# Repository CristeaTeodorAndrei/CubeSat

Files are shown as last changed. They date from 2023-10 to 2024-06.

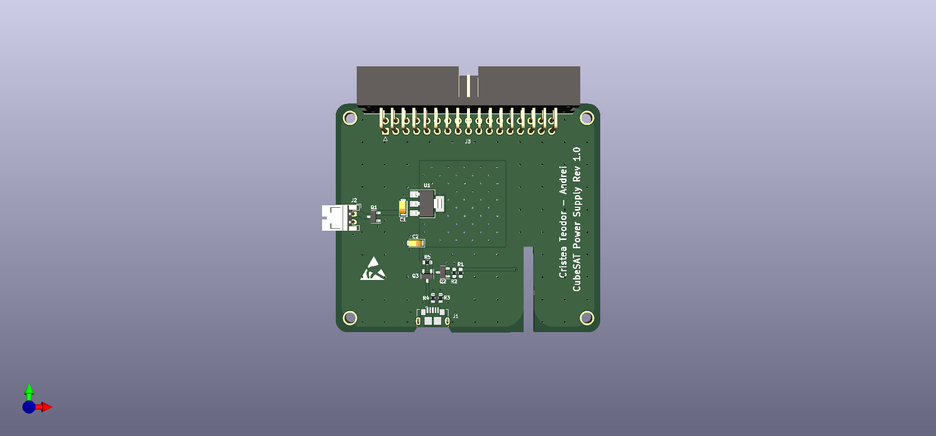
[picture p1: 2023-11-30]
Photos/PSB.png

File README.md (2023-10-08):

# CubeSat

## Introduction

### About CubeSat

A CubeSat is a compact but sophisticated space platform, meticulously engineered to achieve its scientific goals. These miniaturised satellites are created with precision and purpose, representing a cost-effective and efficient approach to space exploration. Their primary role involves specific scientific, technological or educational missions. <br>
Equipped with payloads, sensors and specialised instruments, CubeSats are deployed to collect critical data, monitor phenomena or conduct experiments in space. Their modular nature allows for versatility, enabling CubeSats to address a wide range of research objectives, from observing Earth to studying cosmic phenomena. <br>
They contribute to advancing our understanding of the cosmos, demonstrating that innovation can thrive even within the confines of a compact form factor.

### About the project

The project was developed with the objective of understanding the complexity of space systems, approaching the different problems that arise in this field and solving them in the most energy and cost efficient way. <br>
The future of this project consists in creating a stable platform that allows future improvements so that young students in this domain can develop.

## CubeSat specifications

### Hardware specs

    1. Raspberry PI 4 Model B
    2. MPU6050 Accelerometer and Gyroscope Sensor
    3. BMP280 Pressure Sensor
    4. Raspberry Pi Camera Module 2
    5. NRF20L01 Wireless Module
    6. Battery System UPS 

### Software specs

OBSW was developed in Python, and the operating system on which the software runs is Raspberian on which some software optimizations have been applied.  <br>
The project is structured in 4 phases:

- Activating Remote Control Phase
- Optimization phase
- Testing phase
- OBSW phase

<br>
Each of these phases has a well-defined objective and must be fulfilled before the final code runs.

## Guideline

### Activating Remote Control Phase

Keep in mind that each script that will run will be sent as a command through the GCM. <br>

Power on the GCM, run the script and open the receiver Interface.

- The Interface should prompt a successful connection message.
- A warning message should appear to notify the failure to connect with the OBC. <br>

Power on the OBC.

- Both GREEN and RED LEDs should be ON indicating that OBC is active and ready for requests.
- A succesful connection message should appear on GCM's Interface to ensure that communcations with the OBC is active and can proceed to the optimization phase.

<br>
GCM will try to connect with the OBC every 5 seconds.

### Optimization Phase

In order to reduce energy usage and ensure efficient performance of the whole system, a number of optimizations have been implemented:

- Deactivating Wi-Fi Module
- Deactivating Bluetooth Module
- Deactivating Update Module
- Deactivating UI

By requesting the OBC to run the script <b> Optimization.py</b> via GCM all of those optimizations will be applied and after that the OBC will reboot. <br>
After restarting the system, the GREEN LED will turn ON and RED LED OFF to indicate successful optimization and a confirmation message should appear in GCM's Interface. <br>
<br>
OBC can proceed to the testing phase.

### Testing Phase

By requesting the OBC to run the script <b>Test.py</b>, the OBC begins testing sequence and a custom TM is sent back to the GCM that indicates the sensors has been detected. <br>
If the RFM is not working or is not responding the RED LED will blink continuously.<br>
If the RFM is working the GREEN LED will blink continuously and a TM will be send to the GCM with the following format:

- [0x00, 0x00, 0x00, 0x00]

TM's params should have the following values:

1. (First) 0x00 - MPU6050 has been detected.

- 0x01 - MPU6050 has not been detected.

2. (Second) 0x00 - BMP280 has been detected.

- 0x01 - BMP280 has not been detected.

3. (Third) 0x00 - Camera Module has been detected.

- 0x01 - Camera Module has not been detected.

4. (Fourth) 0x00 - Power supply voltage is nominal.

- 0x05 - The OBC is undervoltage and the power supply should be verified.

<br>
If the TM's values are not nominal OBSW will repeat the test every 5 seconds. <br>
OBC can proceed to the running phase or main code.

### Running phase

In the phase of running the main code all CubeSat components should work according to the parameters.
<br><br>
By requesting the OBC to run the main code <b>OBSW.py</b> nominal TMs should appear in GCM's Interface. <br>
As discussed in the SDCard chapter before the CubeSat leaves the range of the GCM the OBSW will send a warning message that it will soon disconnect and the data will be written locally. 
<br><br>
That's the final state for the CubeSat before the flight. 

### TMTC Format

A nominal TM should have the following format:

- [TimeStamp, Voltage, Temperature, Load, AccX, AccY, AccZ, GyroX, GyroY, GyroZ, Altitude, Pressure]

TM's params should have the following values:

1. <b>TimeStamp</b> [seconds] float (Eg. 1.00) and represent the relative time.
2. <b>Voltage</b> float (Eg. 1.2) and represent the core voltage.
3. <b>Temperature</b>[degrees] float (Eg. 57.01) and represent the OBC's temperature.
4. <b>Load</b> [%] integer (Eg. 5%) and represent the OBC's load.
5. <b>Acceleration{X,Y,Z}</b>[m/s^2] float (Eg. 10.32) and represent the acceleration on each axis.
6. <b>Gyro{X,Y,Z}</b>[deg/s] float (Eg. 11.01) and represent the rotation on each axis.
7. <b>Altitude</b>[meters] integer (Eg. 1100) and represent the altitude of the CubeSat.
8. <b>Pressure</b>[hPa] float (Eg. 1013.89) and represent the pressure applied to the CubeSat. <br>

<br>
One TM is sent every 5 seconds. <br>
Keep in mind that TMTC will only be available for a period of time until the CubeSat moves out of range of the GCM.

### SDCard

Cubesat will have a Raspberry Pi Camera Module 2 connected and the record will be stored on the SD Card. <br>
Because the RFM allows communication over a relatively short distance with the GCM the flight parameters will be stored on the OBC's internal SD Card. <br>
The OBSW will notify the approaching maximum range and detect the loss of GCM connection, and the data will be passed in .txt format. <br>

## Acronyms

- OBSW - OnBoard Software
- UI - User Interface
- OBC - OnBoard Computer
- TMTC - Telemetry/Telecommand
- GCM - Ground Communication Module
- RFM - Radio Frequency Module

## About me

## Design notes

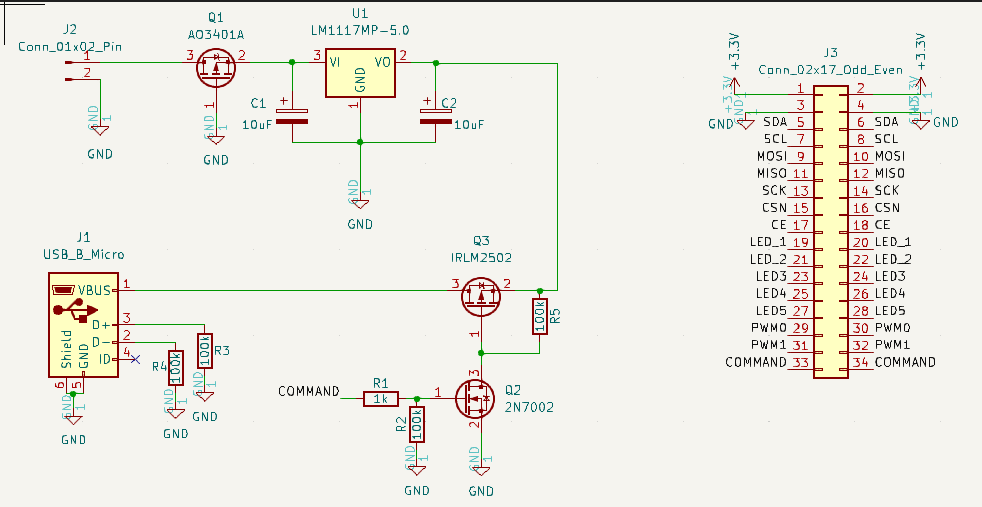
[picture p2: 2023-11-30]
Photos/Schematic_PSB.png

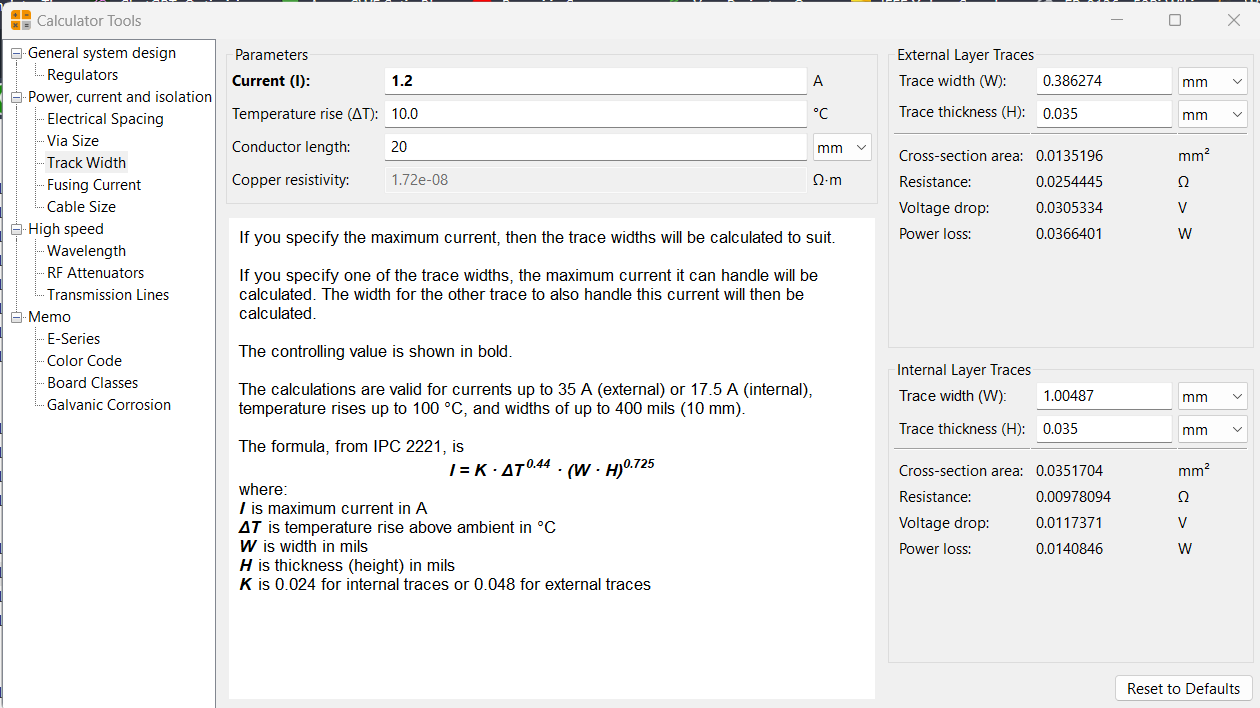
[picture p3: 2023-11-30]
Photos/Power_PSB.png

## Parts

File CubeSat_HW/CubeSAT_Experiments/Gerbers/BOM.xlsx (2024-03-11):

Comment | Designator | Footprint | JLCPCB Part #（optional）
D1 | D1 | LED_0603_1608Metric | C2286
D2 | D2 | LED_0603_1608Metric | C434449
220R | R1 | R_0603_1608Metric | C22962
180R | R2 | R_0603_1608Metric | C22828

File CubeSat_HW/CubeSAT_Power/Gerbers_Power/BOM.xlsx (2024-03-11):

Comment | Designator | Footprint | JLCPCB Part #（optional）
AO3401A | Q1 | SOT-23 | C15127
100k | R4, R3, R2, R5 | R_0603_1608Metric | C25803
LM1117MP-5.0 | U1 | SOT-223-3_TabPin2 | C41202
1k | R1 | R_0603_1608Metric | C21190
10uF | C1, C2 | CP_EIA-3216-18_Kemet-A | C7171
IRLM6402 | Q3 | SOT-23 | C347504
2N7002 | Q2 | SOT-23 | C8545
Micro USB | J1 | Micro USB | C381144

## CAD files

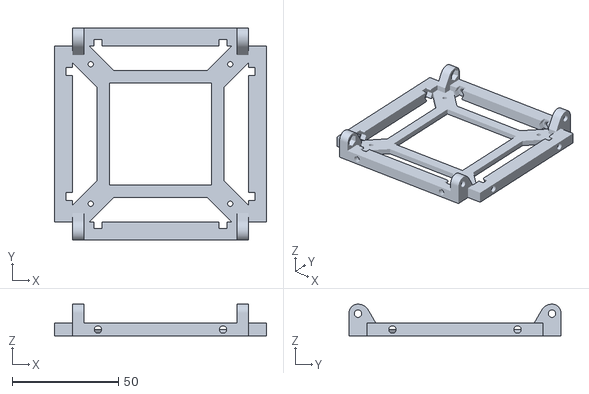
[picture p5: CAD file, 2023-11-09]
CubeSat_3D/Cubesat_Bottom_Frame.stl
100.0 x 100.0 x 15.0

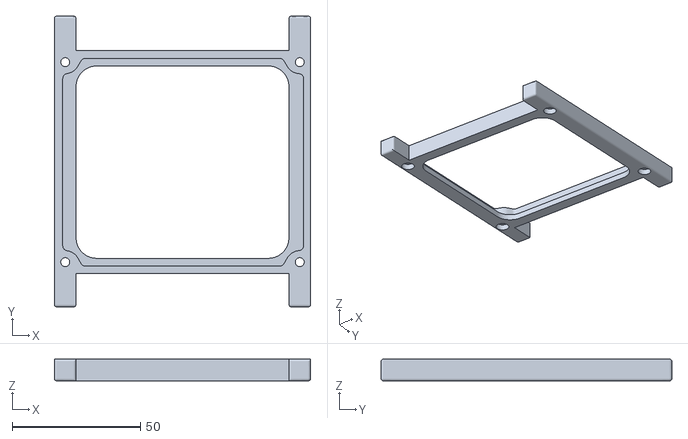
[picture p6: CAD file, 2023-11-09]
CubeSat_3D/Cubesat_Side_Frame_Plain.stl
100.0 x 113.5 x 8.50

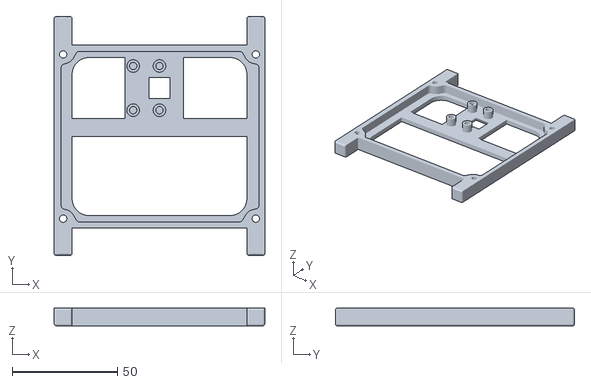
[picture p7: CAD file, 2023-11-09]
CubeSat_3D/Cubesat_RaspbiCam_Frame.stl
100.0 x 113.5 x 8.50

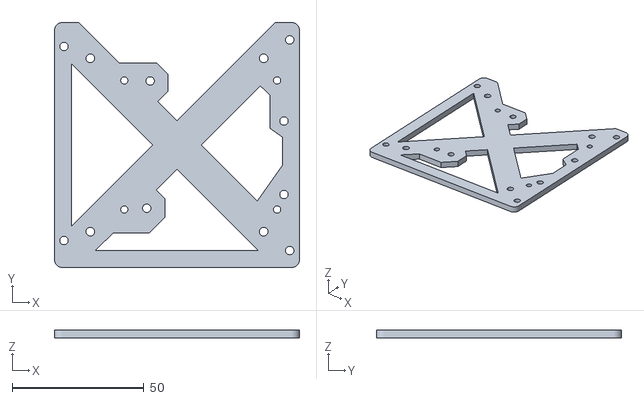
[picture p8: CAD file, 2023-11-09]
CubeSat_3D/Cubesat_Adaptor_Mount.stl
93.0 x 93.0 x 3.00

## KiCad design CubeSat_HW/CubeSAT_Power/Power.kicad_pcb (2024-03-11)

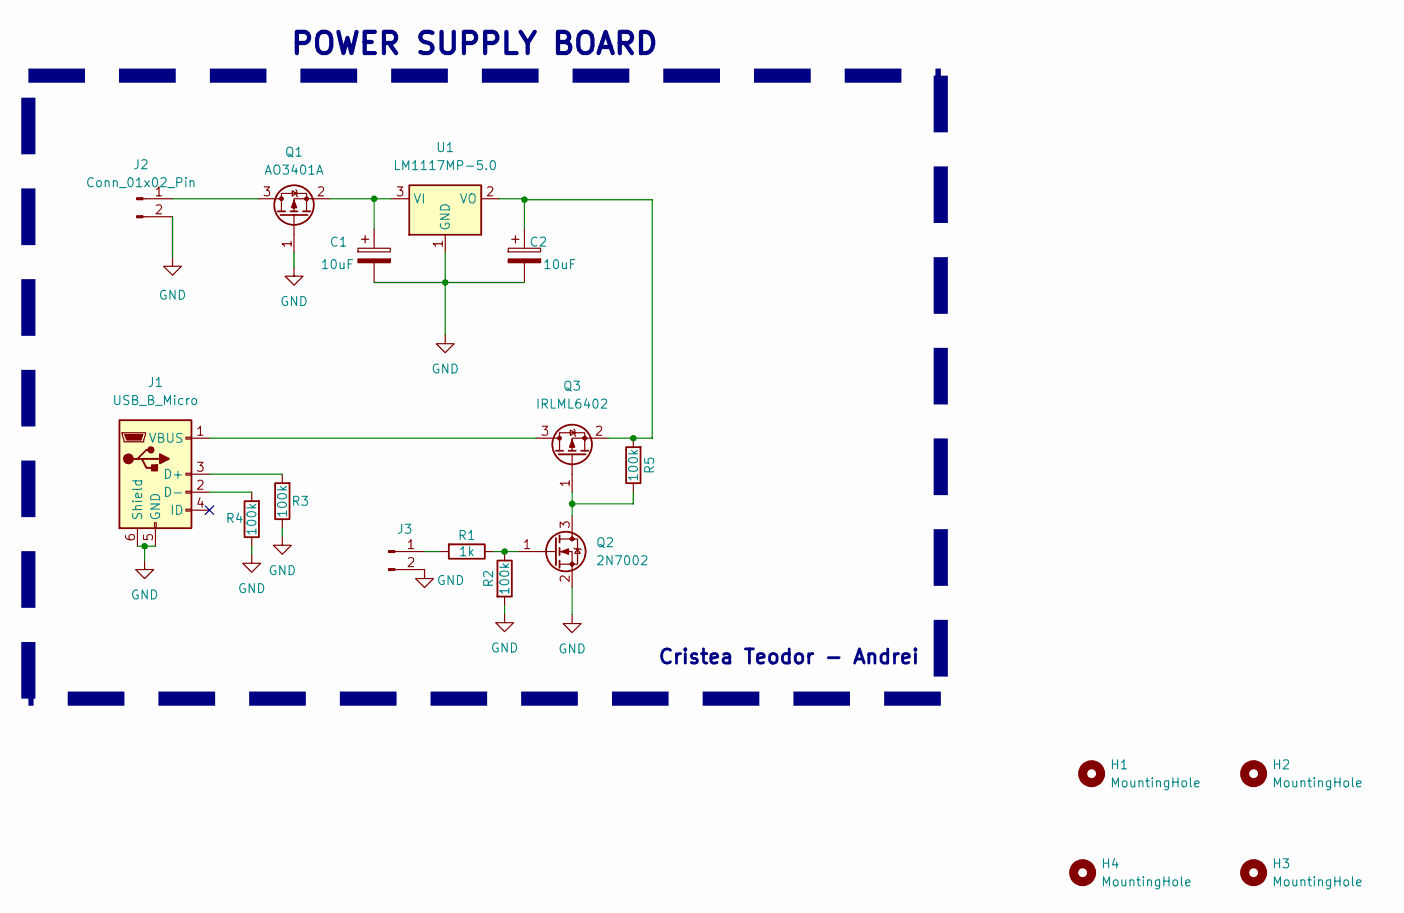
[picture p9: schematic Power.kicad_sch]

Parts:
C1, C2: 10uF; CP_EIA-3216-18_Kemet-A
H1, H2, H3, H4: MountingHole; MountingHole_2.7mm
J1: USB_B_Micro; USB_Micro-B_GCT_USB3076-30-A
J2, J3: Conn_01x02_Pin; PinHeader_1x02_P2.54mm_Vertical
Q1: AO3401A; SOT-23
Q2: 2N7002; SOT-23
Q3: IRLML6402; SOT-23
R1: 1k; R_0603_1608Metric
R2, R3, R4, R5: 100k; R_0603_1608Metric
U1: LM1117MP-5.0; SOT-223-3_TabPin2

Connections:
/COMMAND: J3.1, R1.2
GND: C1.2, C2.2, J1.5 (GND), J1.6 (Shield), J2.2, J3.2, Q1.1 (G), Q2.2 (S), R2.2, R3.1, R4.1, U1.1 (GND)
unnamed: J1.3 (D+), R3.2
unnamed: J1.2 (D-), R4.2
unnamed: J1.1 (VBUS), Q3.3 (D)
unnamed: J2.1, Q1.3 (D)
unnamed: C1.1, Q1.2 (S), U1.3 (VI)
unnamed: Q2.3 (D), Q3.1 (G), R5.1
unnamed: Q2.1 (G), R1.1, R2.1
unnamed: C2.1, Q3.2 (S), R5.2, U1.2 (VO)

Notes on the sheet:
POWER SUPPLY BOARD
Cristea Teodor - Andrei

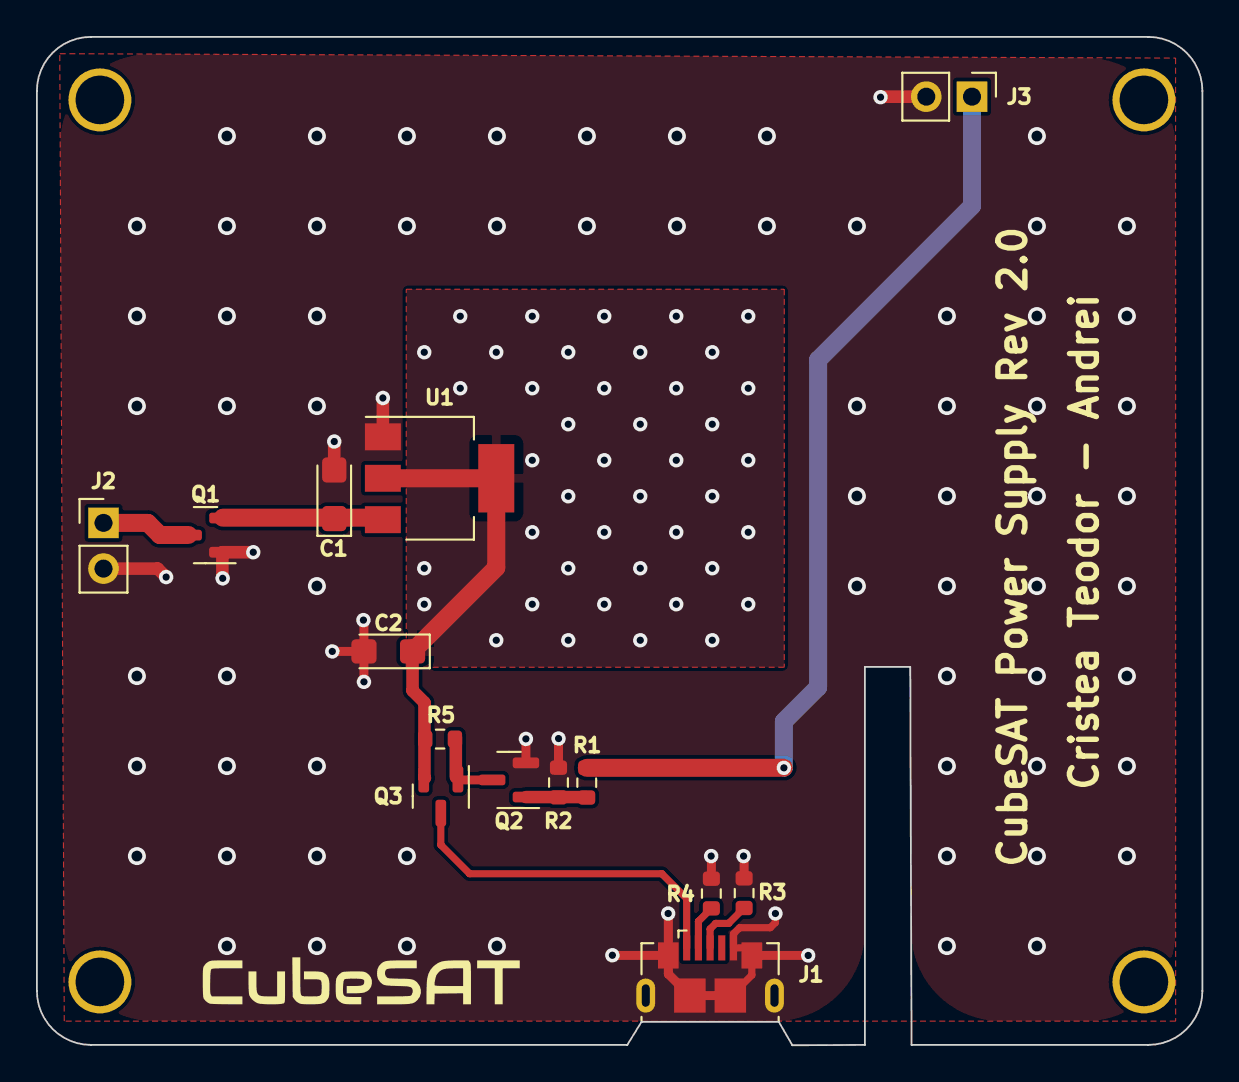
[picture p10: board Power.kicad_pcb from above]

Board: 2 copper layers, 64.7 x 56.0 mm, 18 parts (0 on the bottom side), 10 nets.

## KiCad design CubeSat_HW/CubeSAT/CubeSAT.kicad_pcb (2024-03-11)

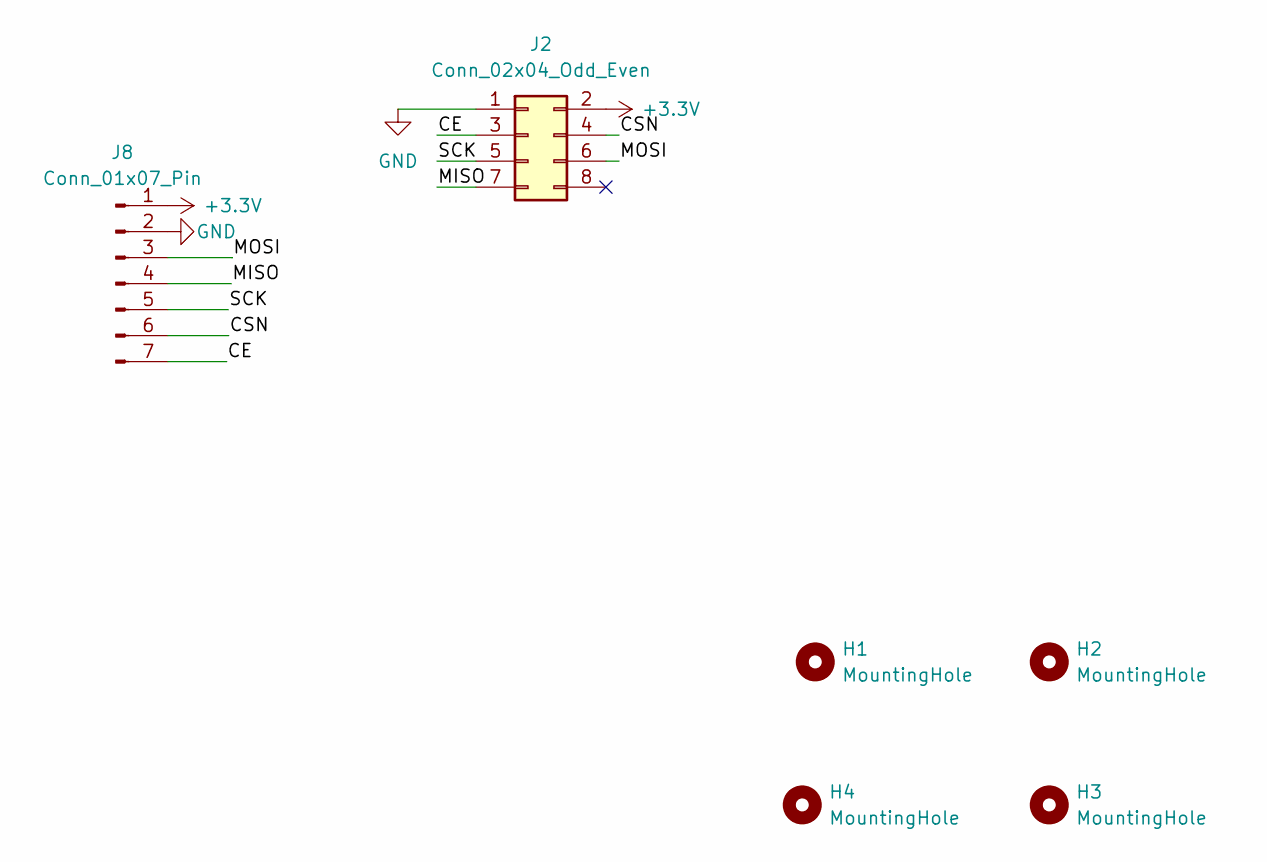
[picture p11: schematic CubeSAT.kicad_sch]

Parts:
H1, H2, H3, H4: MountingHole; MountingHole_2.7mm
J2: Conn_02x04_Odd_Even; PinHeader_2x04_P2.54mm_Vertical
J8: Conn_01x07_Pin; PinHeader_1x07_P2.54mm_Horizontal

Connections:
+3.3V: J2.2, J8.1
/CE: J2.3, J8.7
/CSN: J2.4, J8.6
/MISO: J2.7, J8.4
/MOSI: J2.6, J8.3
/SCK: J2.5, J8.5
GND: J2.1, J8.2

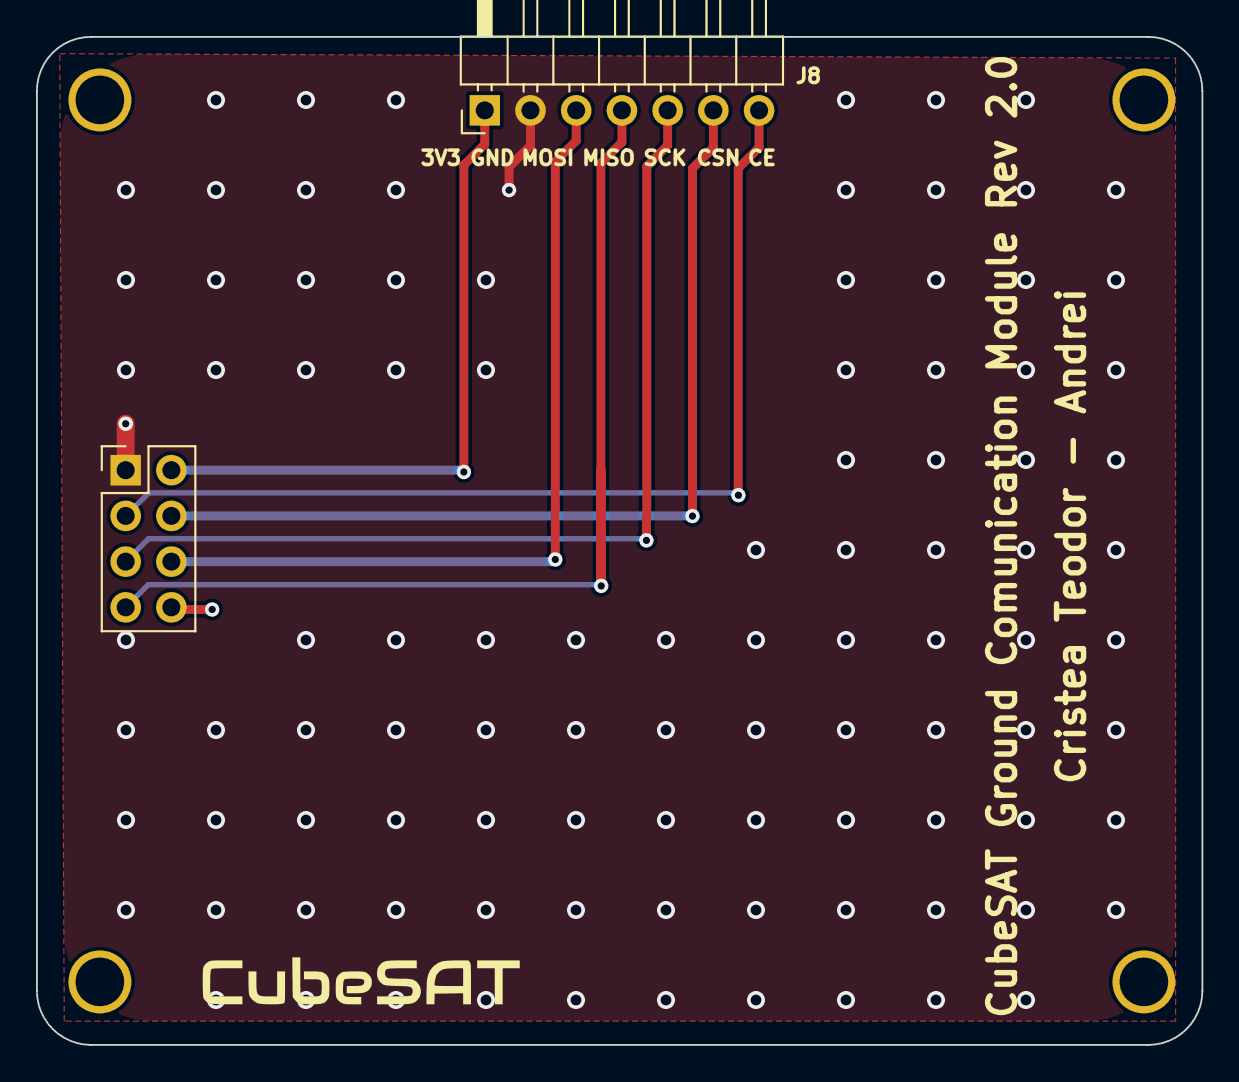
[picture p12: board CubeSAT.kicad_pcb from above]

Board: 2 copper layers, 64.8 x 56.0 mm, 6 parts (0 on the bottom side), 7 nets.

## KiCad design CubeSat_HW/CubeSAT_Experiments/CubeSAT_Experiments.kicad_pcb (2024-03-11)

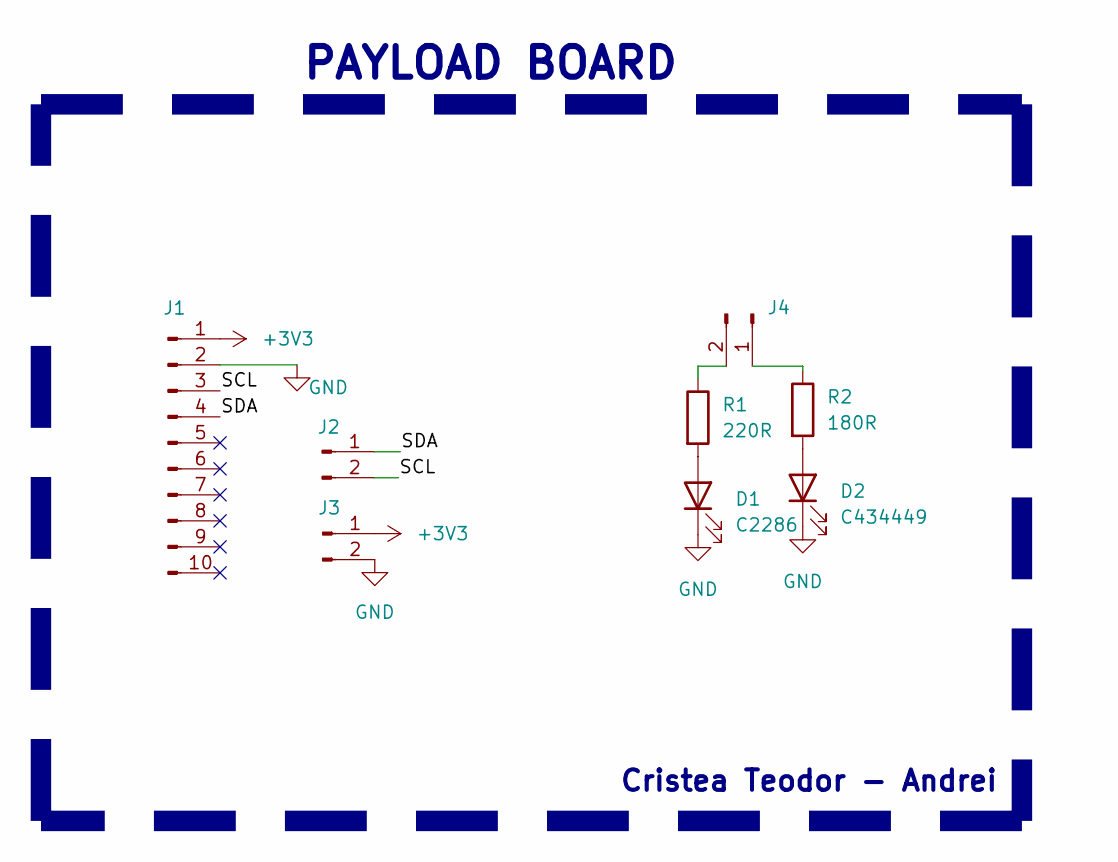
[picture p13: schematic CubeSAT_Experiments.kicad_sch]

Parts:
D1: C2286; LED_0603_1608Metric
D2: C434449; LED_0603_1608Metric
J1: Conn_01x10_Pin; PinHeader_1x10_P2.54mm_Vertical
J2, J3, J4: Conn_01x02_Pin; PinHeader_1x02_P2.54mm_Vertical
R1: 220R; R_0603_1608Metric
R2: 180R; R_0603_1608Metric

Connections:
+3V3: J1.1, J3.1
/SCL: J1.3, J2.2
/SDA: J1.4, J2.1
GND: D1.1 (K), D2.1 (K), J1.2, J3.2
unnamed: D1.2 (A), R1.2
unnamed: D2.2 (A), R2.2
unnamed: J4.1, R2.1
unnamed: J4.2, R1.1

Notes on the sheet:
PAYLOAD BOARD
Cristea Teodor - Andrei

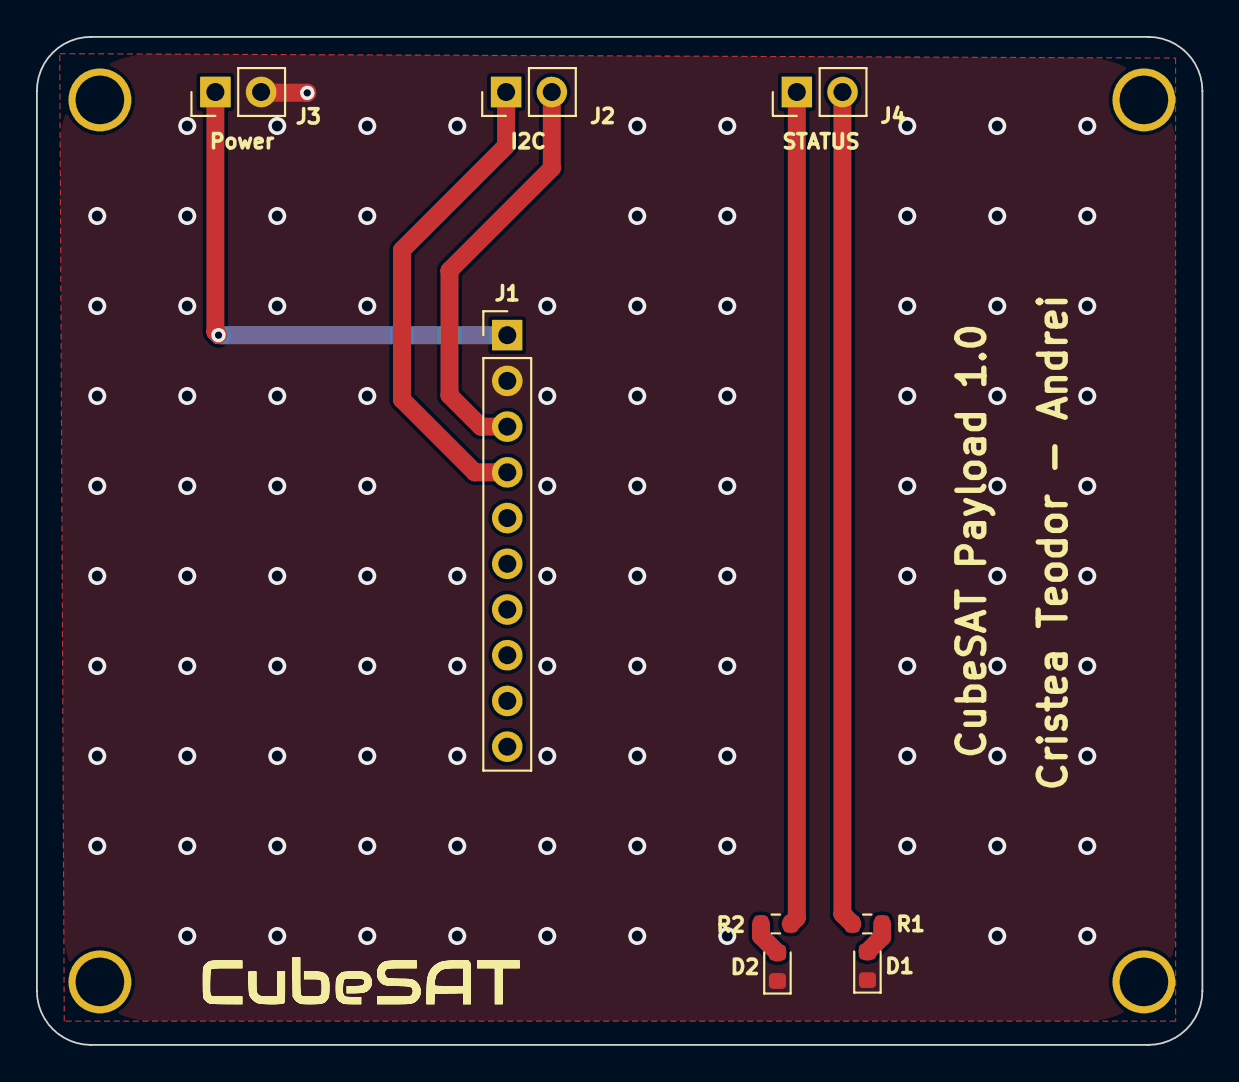
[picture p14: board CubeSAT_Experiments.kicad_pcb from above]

Board: 2 copper layers, 64.8 x 56.0 mm, 12 parts (0 on the bottom side), 8 nets.

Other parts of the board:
H1, H2, H3, H4: MountingHole; MountingHole_2.7mm

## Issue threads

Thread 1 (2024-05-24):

TEST: RAW.py data (000)

CristeaTeodorAndrei, 2024-05-24:
A buffer has been added  and  also an index has been added.
To be tested:
          1. Check if any double chunk are printed in the terminal.
          2. Check if the index has been displayed inside the terminal.

CristeaTeodorAndrei, 2024-05-24:
Everything tested. Another bug found when using the hard restart button. It seems like when doing that the buffer is not clear completely. Solved by using the buffer clear in the lost connection error

Closed 2024-05-24.

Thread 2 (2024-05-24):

TEST: Render.py (001)

CristeaTeodorAndrei, 2024-05-24:
Implemented a 3D Render of the object. I think the main problem is the data speed that arrives to ground.
To be tested:
          1.  The movement with the 3 axis added into the GUI
          2.  Removing the time.sleep(1) from the CubeSAT main function
          3. Store the data into a buffer (TBD)

CristeaTeodorAndrei, 2024-06-06:
Fixed: Removed 3D Render because GUI it's not used anymore

Closed 2024-06-06.

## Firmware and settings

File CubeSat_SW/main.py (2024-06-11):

import time
import struct
from RF24 import RF24, RF24_PA_HIGH
from Sampling import *
import RPi.GPIO as GPIO
import threading

CSN_PIN = 0  
CE_PIN = 22
radio = RF24(CE_PIN, CSN_PIN)
LED1_PIN = 20
LED2_PIN = 21
Charge = 16
GPIO.setmode(GPIO.BCM)
GPIO.setup(LED1_PIN, GPIO.OUT)
GPIO.setup(LED2_PIN, GPIO.OUT)
GPIO.setup(Charge, GPIO.OUT)

if not radio.begin():
    raise RuntimeError("radio hardware is not responding")

address = [b"1Node", b"2Node"]
radio_number = 1
radio.setPALevel(RF24_PA_HIGH)
radio.openWritingPipe(address[radio_number])
radio.payloadSize = 32

def check_battery():
    while True:
        vector = read_sensor_data()
        BAT = vector[-1]
        if BAT < 80:
            GPIO.output(Charge, GPIO.HIGH)
        else:
            GPIO.output(Charge, GPIO.LOW)
        time.sleep(100)

def main():
    radio.stopListening()
    while True:
        vector = read_sensor_data()
        #print("Sensor Data:", vector)
        
        first_part = struct.pack("<8f", *vector[:8])
        start_timer = time.monotonic_ns()
        result1 = radio.write(first_part)
        end_timer = time.monotonic_ns()
        total_time_ms = (end_timer - start_timer) / 1000000
        #print(f"Transmission Time: {total_time_ms} ms")
        second_part = struct.pack("<8f", *vector[8:], total_time_ms)
        result2 = radio.write(second_part)

        if not result1 or not result2:
            #print("Transmission failed or timed out")
            GPIO.output(LED2_PIN, GPIO.HIGH)
            time.sleep(0.5)
            GPIO.output(LED2_PIN, GPIO.LOW)
        else:
            #print("Full vector transmitted! Time to Transmit:", f"{total_time_ms} ms. Sent: {vector}")
            GPIO.output(LED1_PIN, GPIO.HIGH)
            time.sleep(0.5)
            GPIO.output(LED1_PIN, GPIO.LOW)
            
        time.sleep(0.5)  # Small delay to help with synchronization

if __name__ == "__main__":
    try:
        battery_thread = threading.Thread(target=check_battery)
        battery_thread.daemon = True
        battery_thread.start()
        main()
    except KeyboardInterrupt:
        #print("Keyboard Interrupt detected. Powering down radio.")
        radio.powerDown()
        GPIO.cleanup()

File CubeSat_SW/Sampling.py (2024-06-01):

import psutil
import time
import smbus2
import RPi.GPIO as GPIO

MPU9250_ADDRESS = 0x68
MPU9250_ACCEL_XOUT_H = 0x3B
MPU9250_ACCEL_YOUT_H = 0x3D
MPU9250_ACCEL_ZOUT_H = 0x3F
MPU9250_GYRO_XOUT_H = 0x43
MPU9250_GYRO_YOUT_H = 0x45
MPU9250_GYRO_ZOUT_H = 0x47
MPU9250_MAG_XOUT_L = 0x03
MPU9250_MAG_XOUT_H = 0x04
MPU9250_MAG_YOUT_L = 0x05
MPU9250_MAG_YOUT_H = 0x06
MPU9250_MAG_ZOUT_L = 0x07
MPU9250_MAG_ZOUT_H = 0x08
MPU9250_TEMP_OUT_H = 0x41
MPU9250_TEMP_OUT_L = 0x42
_REG_CONFIG = 0x00
_REG_SHUNTVOLTAGE = 0x01
_REG_BUSVOLTAGE = 0x02
_REG_POWER = 0x03
_REG_CURRENT = 0x04
_REG_CALIBRATION = 0x05

bus = smbus2.SMBus(1)
GPIO.setmode(GPIO.BCM)

class BusVoltageRange:
    RANGE_16V = 0x00
    RANGE_32V = 0x01

class Gain:
    DIV_1_40MV = 0x00
    DIV_2_80MV = 0x01
    DIV_4_160MV = 0x02
    DIV_8_320MV = 0x03

class ADCResolution:
    ADCRES_9BIT_1S = 0x00
    ADCRES_10BIT_1S = 0x01
    ADCRES_11BIT_1S = 0x02
    ADCRES_12BIT_1S = 0x03
    ADCRES_12BIT_2S = 0x09
    ADCRES_12BIT_4S = 0x0A
    ADCRES_12BIT_8S = 0x0B
    ADCRES_12BIT_16S = 0x0C
    ADCRES_12BIT_32S = 0x0D
    ADCRES_12BIT_64S = 0x0E
    ADCRES_12BIT_128S = 0x0F

class Mode:
    POWERDOW = 0x00
    SVOLT_TRIGGERED = 0x01
    BVOLT_TRIGGERED = 0x02
    SANDBVOLT_TRIGGERED = 0x03
    ADCOFF = 0x04
    SVOLT_CONTINUOUS = 0x05
    BVOLT_CONTINUOUS = 0x06
    SANDBVOLT_CONTINUOUS = 0x07

class INA219:
    def __init__(self, i2c_bus=1, addr=0x40):
        self.bus = smbus2.SMBus(i2c_bus)
        self.addr = addr
        self._cal_value = 0
        self._current_lsb = 0
        self._power_lsb = 0
        self.set_calibration_16V_5A()

    def read(self, address):
        data = self.bus.read_i2c_block_data(self.addr, address, 2)
        return (data[0] * 256) + data[1]

    def write(self, address, data):
        temp = [0, 0]
        temp[1] = data & 0xFF
        temp[0] = (data & 0xFF00) >> 8
        self.bus.write_i2c_block_data(self.addr, address, temp)

    def set_calibration_16V_5A(self):
        self._current_lsb = 0.1524  # Current LSB = 100uA per bit
        self._cal_value = 26868
        self._power_lsb = 0.003048  # Power LSB = 2mW per bit
        self.write(_REG_CALIBRATION, self._cal_value)
        self.bus_voltage_range = BusVoltageRange.RANGE_16V
        self.gain = Gain.DIV_2_80MV
        self.bus_adc_resolution = ADCResolution.ADCRES_12BIT_32S
        self.shunt_adc_resolution = ADCResolution.ADCRES_12BIT_32S
        self.mode = Mode.SANDBVOLT_CONTINUOUS
        self.config = (
            self.bus_voltage_range << 13
            | self.gain << 11
            | self.bus_adc_resolution << 7
            | self.shunt_adc_resolution << 3
            | self.mode
        )
        self.write(_REG_CONFIG, self.config)

    def getShuntVoltage_mV(self):
        self.write(_REG_CALIBRATION, self._cal_value)
        value = self.read(_REG_SHUNTVOLTAGE)
        if value > 32767:
            value -= 65535
        return value * 0.01

    def getBusVoltage_V(self):
        self.write(_REG_CALIBRATION, self._cal_value)
        self.read(_REG_BUSVOLTAGE)
        return (self.read(_REG_BUSVOLTAGE) >> 3) * 0.004

    def getCurrent_mA(self):
        value = self.read(_REG_CURRENT)
        if value > 32767:
            value -= 65535
        return value * self._current_lsb

    def getPower_W(self):
        self.write(_REG_CALIBRATION, self._cal_value)
        value = self.read(_REG_POWER)
        if value > 32767:
            value -= 65535
        return value * self._power_lsb

def read_word(reg):
    high = bus.read_byte_data(MPU9250_ADDRESS, reg)
    low = bus.read_byte_data(MPU9250_ADDRESS, reg + 1)
    value = (high << 8) + low
    return value

def read_cpu_temperature():
    try:
        with open('/sys/class/thermal/thermal_zone0/temp', 'r') as f:
            temp = int(f.read()) / 1000.0
            return temp
    except FileNotFoundError:
        return None

def convert_accel(raw_value):
    sensibility = 2.0 / 32768.0
    return raw_value * sensibility

def convert_gyro(raw_value):
    sensibility = 500.0 / 32768.0
    return raw_value * sensibility

def convert_mag(raw_value):
    sensibility = 4800.0 / 32768.0
    return raw_value * sensibility

def read_sensor_data():
    ina219 = INA219(i2c_bus=1, addr=0x43)
    bus_voltage = ina219.getBusVoltage_V()
    current = -ina219.getCurrent_mA()
    power = ina219.getPower_W()
    p = (bus_voltage - 3) / 1.2 * 100
    accel_x = read_word(MPU9250_ACCEL_XOUT_H)
    accel_y = read_word(MPU9250_ACCEL_YOUT_H)
    accel_z = read_word(MPU9250_ACCEL_ZOUT_H)
    gyro_x = read_word(MPU9250_GYRO_XOUT_H)
    gyro_y = read_word(MPU9250_GYRO_YOUT_H)
    gyro_z = read_word(MPU9250_GYRO_ZOUT_H)
    mag_x = read_word(MPU9250_MAG_XOUT_L)
    mag_y = read_word(MPU9250_MAG_YOUT_L)
    mag_z = read_word(MPU9250_MAG_ZOUT_L)

    vector = [
        round(read_cpu_temperature(), 3),
        round(psutil.cpu_percent(), 3),
        round(bus_voltage, 3),
        round(current / 1000, 3),
        round(power, 3),
        round(convert_accel(accel_x), 3),
        round(convert_accel(accel_y), 3),
        round(convert_accel(accel_z), 3),
        round(convert_gyro(gyro_x), 3),
        round(convert_gyro(gyro_y), 3),
        round(convert_gyro(gyro_z), 3),
        round(convert_mag(mag_x), 3),
        round(convert_mag(mag_y), 3),
        round(convert_mag(mag_z), 3),
        round(p, 3)
    ]

    return vector

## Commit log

2023-10-16 Added hardware project
    [CubeSAT.kicad_pcb, CubeSAT.kicad_sch]
2023-10-30 Added version 2 of the PCB
    [CubeSAT-B_Cu.gbl, CubeSAT-B_Mask.gbs, CubeSAT-B_Paste.gbp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]
2023-11-09 feat: Added 3D files for the CubeSAT
    [Cubesat_Adaptor_Mount.stl, Cubesat_Bottom_Frame.stl, Cubesat_RaspbiCam_Frame.stl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]
2023-11-09 feat: Added Power and Com PCB
    [CubeSAT-B_Cu.gbl, CubeSAT-B_Mask.gbs, CubeSAT-B_Paste.gbp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]
2023-11-14 feat: Added new version for the Power Supply Board
    [Power.kicad_pcb, Power.kicad_sch]
2023-11-18 fix: Minor fixes to the Power Supply Board
    [CubeSAT-B_Cu.gbl, CubeSAT-B_Mask.gbs, CubeSAT-B_Silkscreen.gbo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]
2023-11-18 release: Added version II of PS project.
    [Power.kicad_pcb, Power.kicad_sch]
2023-11-18 feat: Added GBR, CPL and BOM for PS Board
    [BOM.xlsx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]
2023-11-18 feat: Added new version for HW Board
    [CubeSAT.kicad_pcb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]
2023-11-30 feat: Minor changes
    Created a special test case to verify if the service has been disabled or not.
2023-11-30 feat: Added GBR, BOM, CPL files for the project
    [BOM.xlsx, CubeSAT.kicad_pcb, CubeSAT.kicad_sch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]
2023-11-30 fix: Small changes
    [Power.kicad_pcb, Power.kicad_sch]
2023-11-30 fix: The user cannot see the events for testing
    [Optimization.py]
2023-11-30 fix: Wrong function parameter sent
    [Optimization.py]
2023-11-30 fix: Set the python installer to quiet mode.
    [Optimization.py]
2023-11-30 fix: Set the optimize to return the error code, not the entire line
    [Optimization.py]
2023-11-30 fix: Minor visual changes
    [Optimization.py]
2023-11-30 feat: Added rebooting condition
    [Optimization.py, main.py]
2023-11-30 fix: Trying to fix VM restarting error
    [Optimization.py]
2023-11-30 fix: Trying to solve VM restarting error
    [Optimization.py]
2023-11-30 fix: Rebased (try #0)
    [Optimization.py]
2023-11-30 fix: Rebase (try #1)
    [Optimization.py]
2023-11-30 fix: Rebase (#try 2)
    [Optimization.py]
2023-12-01 fix: Fixing Updates function
    [Optimization.py]
2023-12-01 fix: Fixed Bluetooth function
    [Optimization.py]
2023-12-01 fix: Fixed GUI function
    [Optimization.py]
2023-12-01 feat: Trying to fix GUI crashing error.
    [Optimization.py]
2023-12-01 fix: Removed the terminal infos
    [Optimization.py]
2023-12-01 fix: Trying to fix GUI error (#000)
    [Optimization.py]
2023-12-01 fix: Trying to fix GUI error (#001)
    [Optimization.py]
2023-12-01 fix: Trying to fix GUI error (#002)
    [Optimization.py]
2023-12-01 release: Fixed GUI problem! {Explanation}
    [Optimization.py]
2023-12-01 feat: Trying to add reboot condition.
    [Optimization.py]
2023-12-01 fix: Trying to add Reboot condition
    [Optimization.py]
2023-12-01 Release: Optimization stage finished (#000)
    COMM PROTOCOLS and DISABLE WI-FI have been commented because I cannot emulate them in VM.
    Future testing phases should be done.
2024-03-11 feat: Added Payload Board and new Gerbers for the project
    [BOM.xlsx, CubeSAT.kicad_pcb, CubeSAT.kicad_sch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]
2024-03-11 fix: Fixed indentation in the code for better view
    [Optimization.py]
2024-05-23 fix: Updated the Ping to run much faster
    [Ping.py]
2024-05-23 fix: Updated GUI.py with new buttons
    [GUI.py]
2024-05-24 feat: Updated the Raw.py
    Fixed a bug that prevents the buffer to get empty after a lost connection.
    [Raw.py]
2024-05-25 Release: Fixed a bug inside the code
    [Ping.py]
